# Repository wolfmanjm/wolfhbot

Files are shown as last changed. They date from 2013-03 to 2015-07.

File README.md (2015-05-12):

Wolf CoreXY
============

_NOTE_ This is still a work in progess, it is currently printing quite well.
_UPDATE_ Changed the Y rails to Makerslide and Makeslide carriages and VWheels.

A large build volume 3d printer based on the CoreXY concept.

It uses 2020 Misumi extrusions for most of the frame.

* The X carriage runs on 2020 and openrail from openbuilds.com
* The Y carraiges run on Makerslide from Inventables.com
* The drive can use either 65lb Spectra fishing line and machined spools, or GT2 pulleys and belts
* the Belts have no corss over, they are stacked on top of eachother instead
* build volume is around 12 inches cubed (300x300x300 mm)
* The Z platform has one Z actuator made of 2040 vslot
  and a printed carriage. It runs on an ACME 1/2" leadscrew with 10TPI and a printed PLA Nut
  and uses a moving knot to keep the cantilever level
* The X carriage is printable but is best milled from MDF

Pictures and Videos
-------------------

* [first movements](http://youtu.be/cA50g_V9wbQ)
* [second movement](http://youtu.be/p5AFRTE33c4)
* [Drawing big circle](http://youtu.be/9L7iuisqjXY)
* [Insane speed circle](http://youtu.be/wYBltiACMb0)
* [New Z actuator](http://flic.kr/p/gcBkjw)
* [New Z actuator](http://flic.kr/p/gcBGvX)
* [Printing vase](http://youtu.be/nGm1CWDJkY0)
* [Corexy Belt no cross over](http://flic.kr/p/iT5DkX)
* [Corexy Belt no cross over](http://flic.kr/p/iT7Lpm)
* [Corexy Belt no cross over](http://flic.kr/p/iT73UX)

For historical purposes...

* [animation of the scissor lift concept](http://blog.wolfman.com/files/scissor-lift.gif)
* [Scissor Lift prototype in action](http://youtu.be/5y0PBw3Y6yg)

Recently re wired to be Corexy rather than HBot. This seems to reduce
racking of the X Gantry. [See](http://joshuavasquez.com/docs/jVasquez/Projects/coreXY.html)

I see no difference between using Spectra line drive and GT2 belts, in
fact if anything it was slightly smoother using the line drive.

Spectra Drive
--------------
For Spectra drive the four idlers on the XGantry are grooved 5mm bearings that bolt
directly to the extrusion slots. One of the X carriage bearings is
raised 10mm to keep the lines parallel.

The four end idlers are grooved 5mm bearings that are screwed directly
into the tapped center of the vertical extrusion. This provides very
solid idlers than can take the tension of the spectra when it is
tight.  The grooves are necessary otherwise the spectra just runs off
the top or bottom of the bearing.
These bearings are stacked on top of each other with a
washer in between, this allows the cables to run on top of each other
and no cross over is needed.

GT2 Belt Drive
--------------
The two end idlers are 2x flanged bearings back to back, and another pair separated with a washer above it,
Then two of the idlers on the X Gantry are raised to keep the belt riding level.
I avoid the cross over of the belts by running the two belts one above the other in parallel.

Z Bed
-----

The scissor lift idea was nice but the prototype showed that a Nema17
did not have enough torque to lift the bed.  I think the bottom of the
scissor lift needs to lift 4 times the weight so any pressure on the
top caused the motor to skip.

The new Z actuator is a length of 500mm of 2040 VSlot, with a printed
carriage and v wheels. Driven by a McMaster ACME 1/2" leadscrew with
10TPI, Bearing blocks using 608 at top and bottom and a Nema17 with
5mm/0.25" flexible coupling. The bottom bearing block isolates the
flexible coupling from taking any weight and compressing. As the 1/2"
leadscrew is pretty big it has no wobble as far as I can tell and
having bearings top and bottom seems to be very stable. I also used a
printed Leadscrew nut printed in PLA and it seems pretty snug and
smooth. I also used a half height leadscrew nut and spring to implement
antibacklash which appears to be necessary.

There is a length of 2040 that spans from the Z actuator to the other
side of the frame where another 500mm length of 2040 VSlot has a vslot
mini carriage which is bolted to the end of the 2040 beam. Halfway
along this beam is a short piece of 2020 perpendicular to it, this
provides the third attachment point for the bed.

The most important part of this design is the
[moving knot](http://cockrum.net/cnc_mechanical.html), which is attached to
the top and bottom and runs over 4 v groove bearings on the cross
beam, This keeps the beam level while allowing a single actuator on one
end to move it up and down. This is the [far end](http://flic.kr/p/i67Sim),
and here is a view of the [whole assembly](http://flic.kr/p/i67Es7).

The bed is attached to the cross beam at three places to provide three
point bed levelling.  I use a scheme where a 4mm stud is screwed into
the tslots, and a 25mm length of aluminum rod, tapped to 4mm is
screwed onto that, this can be turned to move up and down the stud. At
the top of the aluminum is a cut out that the glass bed fits. Next to
this, and also bolted into the tslot, is an M4 bolt with a conical
spring bolted to the top, this pushes the glass at the three
attachment points up into the slots on the aluminum rounds. This keeps
the glass flat without deforming it, and allows it to be leveled at
three points by turning the aluminum rounds. Some jam nuts are used
to screw up to the aluminum rounds to stop them unscrewing once
levelled.

So this adds several printed parts... The Carriage, a bracket to hold
the leadscrew nut, and bearing blocks. Also some lathe work to cut a
thread into the center of some 1/2" aluminum round, and lathe a groove
at the top that the glass can slot into. (If the bed is not heated
this could be a printed part).

BOM
---
Aluminum parts are from Misumi with Misumi part numbers

* 10x 500mm HFS2020 20mm extrusions - frame
* 16x HBLFSN5 corner brackets - frame
* 2x  550mm HFS2020 - X Gantry sides
* 2x  85mm HFS2020 - X Gantry sides (Note it's cheaper to buy 2x 1000mm of 2020 and cut these yourself)
* 2x  540mm Makerslide - Y Rails
* 4x  HBLFSNF5 brackets - X Gantry
* 1x  500mm HFS2040 - Z Bed
* 1x  250mm HFS2020 - Z Bed
* 2x  Shapeoko motor mounts https://www.inventables.com/technologies/upgraded-shapeoko-motor-mount - Y carriages
* 12x VWheels https://www.inventables.com/technologies/dual-bearing-v-wheel-kit or http://openbuildspartstore.com/delrin-v-wheel-kit/
* lots of M5 nuts and bolts
* lots of M3 nuts and bolts
* 2x Nema 17 Stepper motors (preferably Kysan or equivalent)

Spectra drive
-------------
* 2x  Delrin Spools for [Spectra](http://3d.grabercars.com/?product=filament-drive-reel-grooved-delrin-18mm-o-d-for-kossel) or any of the spools he sells at http://3d.grabercars.com/?post_type=product
* 8x  625VV grooved bearings - for idlers from [ebay](http://www.ebay.com/itm/10-5-16-5mm-625VV-5mm-V-Groove-Guide-Pulley-Sealed-Rail-Ball-Bearing-5-16-5-/170998886188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)
* several yards of 65lb Spectra fishing line (Powerpro)
* 2x ball swivels from a fishing store

OR

Belt Drive
----------
* 10 meters GT2 belt
* 2 x GT2 pulleys 20 tooth
* 12 x 5mm flanged bearings for the idlers 

Printed Parts
-------------
* 1x motor-bracket-l.stl
* 1x motor-bracket-r.stl
* 1x x-carriage.stl

Z bed
-----
* 1x Nema 17
* 1x lead screw (McMaster 1/2" 10TPI ACME)
* Two printed Leadscrew nuts and a collar for the anti backlash
* 5/8" diameter spring for the anti backlash
* 2x 500mm 2040 VSlot
* 4x solid V Wheels http://openbuildspartstore.com/solid-v-wheel-kit/
* 1x printed Z carriage, plus leadnut holder
* 1x mini vslot carriage and mini wheels http://openbuildspartstore.com/mini-v-wheel-plate/
* 4x v groove bearings, 2x turnbuckles, two lengths of Spectra fishing line for the moving knot

Construction
------------

Getting the top of the frame square is essential, measure each end of the Y
rails to make sure they are parallel. Next the belts need to have exactly the
same tension to keep the X gantry straight, this was introducing non-square
prints for me. Loosen the X gantry on both Y carriages so it sits loosely on
the Y carriages, then measure the distance of each end of the X Gantry to the
front corner of the frame. Now tighten one or other belt until the X Gantry is
square to the Y rails, then tighten it down to the Y carriages.

If you find cylinders print out oblong or squares are not square this is
probably the problem.

License
-------

CC BY SA

<br /><span xmlns:dct="http://purl.org/dc/terms/" property="dct:title">WolfHBot</span> by <a xmlns:cc="http://creativecommons.org/ns#" href="http://wolfmanjm.github.com/wolfhbot" property="cc:attributionName" rel="cc:attributionURL">Jim Morris</a> is licensed under a <a rel="license" href="http://creativecommons.org/licenses/by-sa/3.0/deed.en_US">Creative Commons Attribution-ShareAlike 3.0 Unported License</a>.<br />Based on a work at <a xmlns:dct="http://purl.org/dc/terms/" href="https://github.com/wolfmanjm/wolfhbot" rel="dct:source">https://github.com/wolfmanjm/wolfhbot</a>.

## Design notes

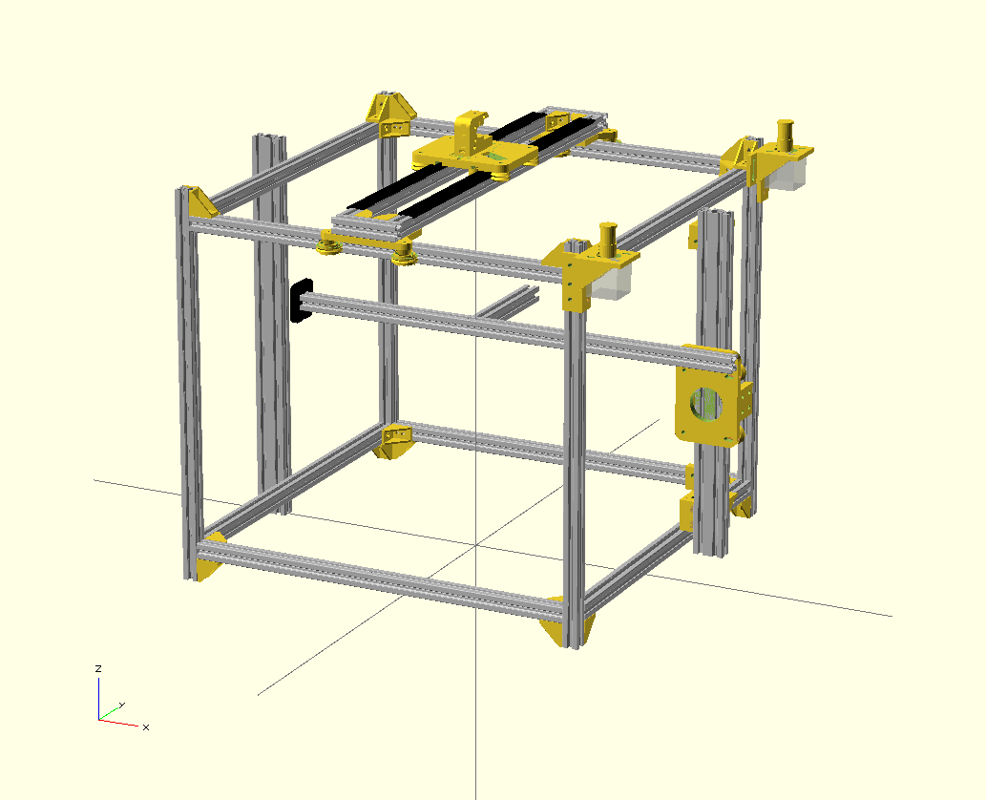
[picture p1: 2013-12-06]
pics/corexy-frame.png

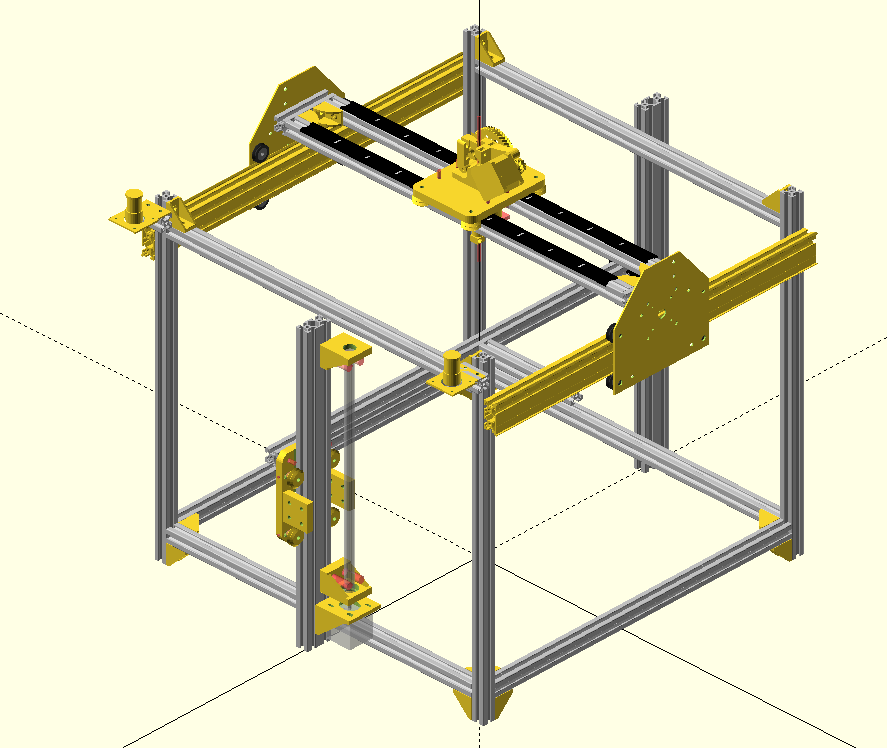
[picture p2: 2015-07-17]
pics/new-gantry.png

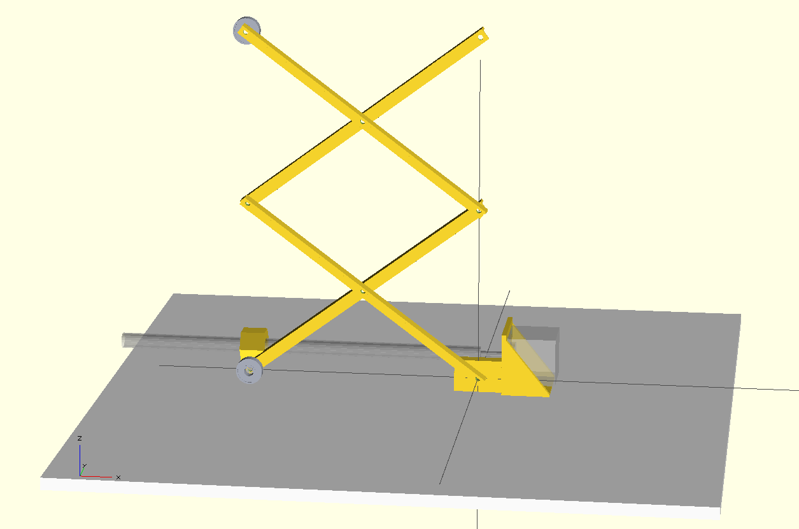
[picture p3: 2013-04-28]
pics/scissor-lift.png

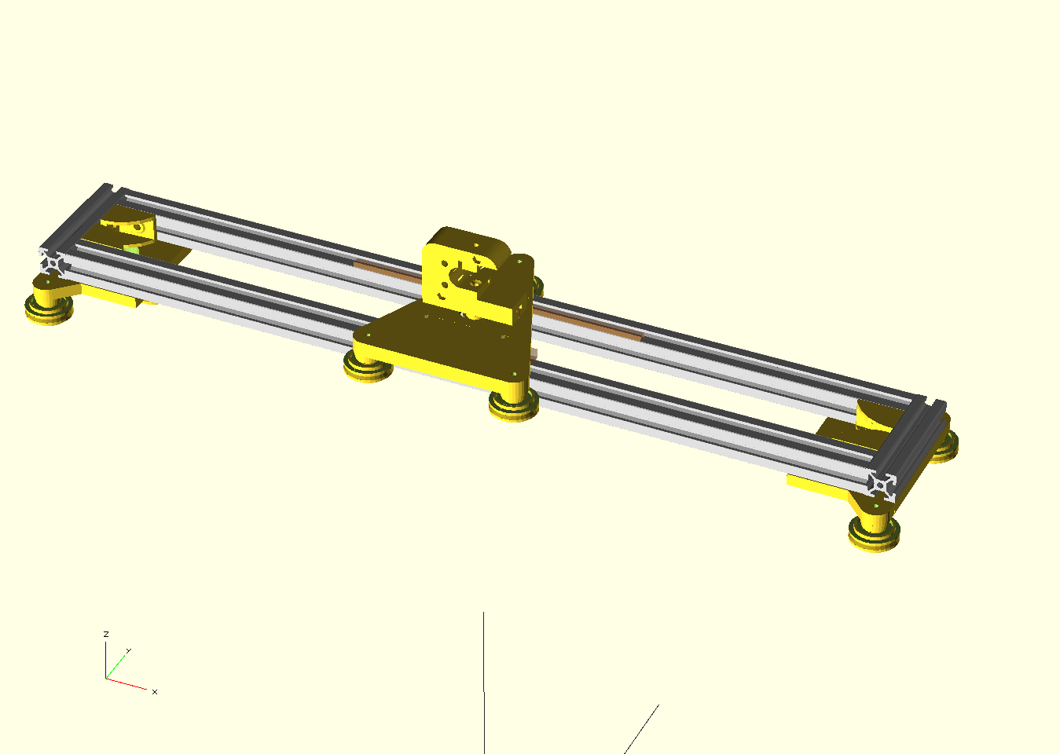
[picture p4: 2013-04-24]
pics/XYGantry.png

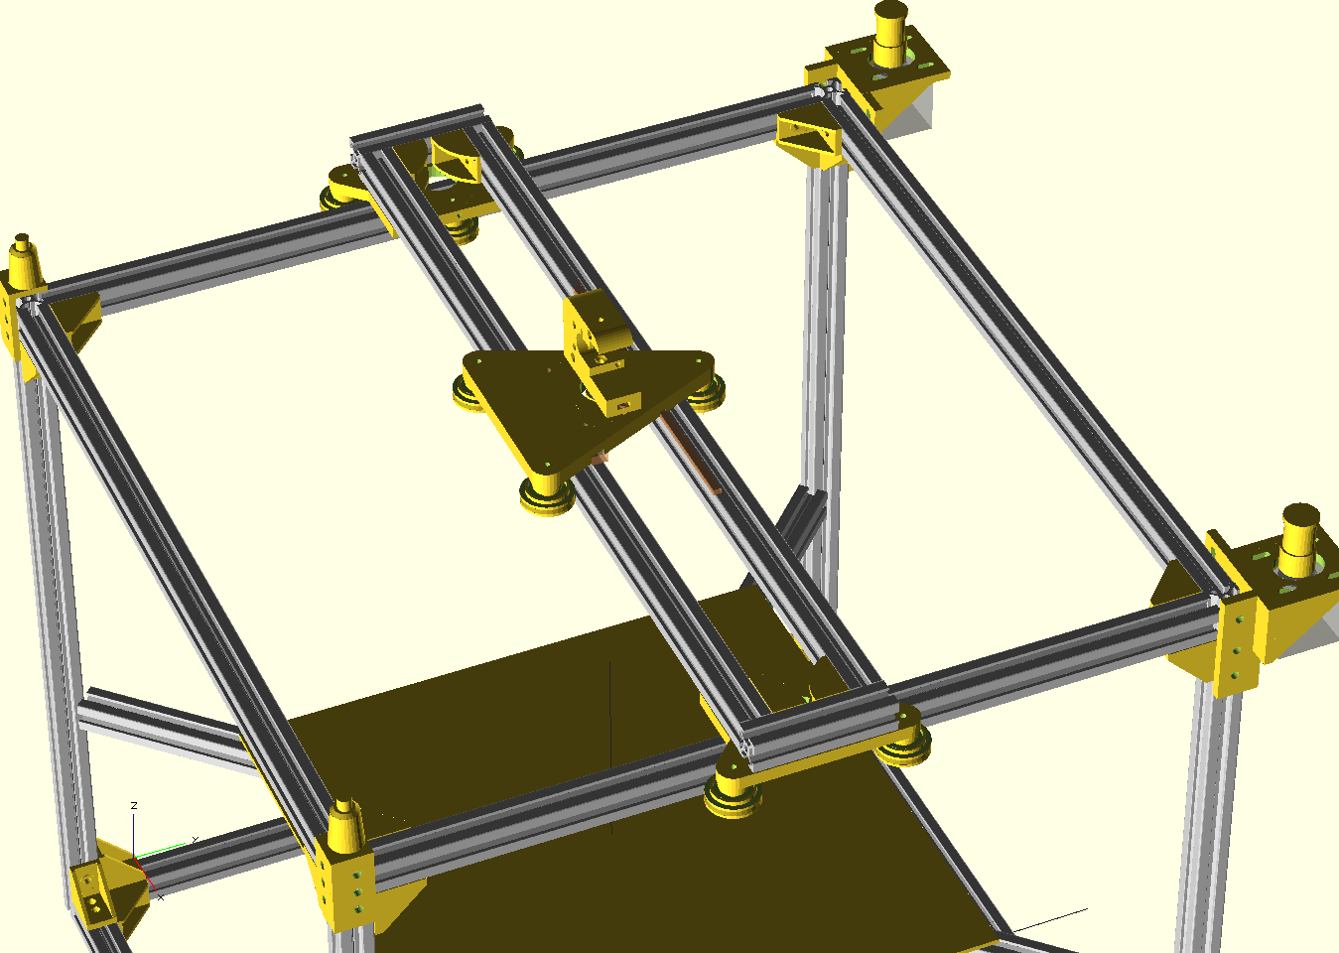
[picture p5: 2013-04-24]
pics/topview.png

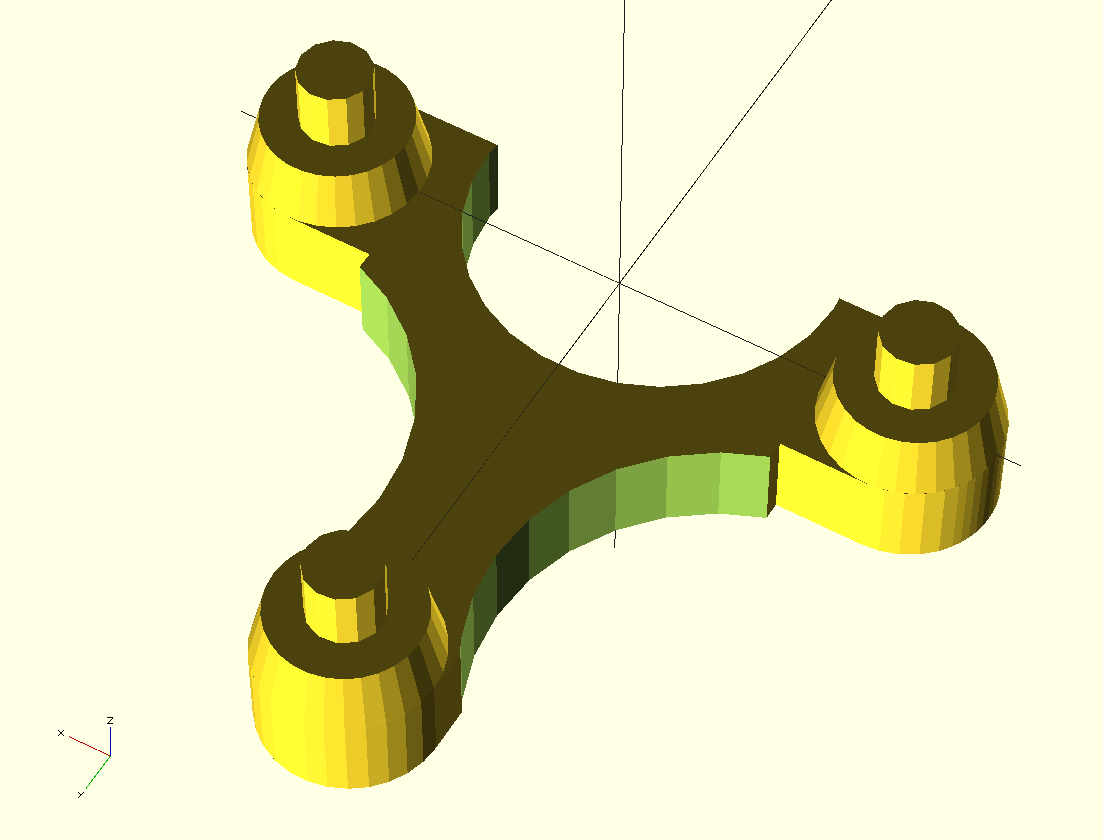
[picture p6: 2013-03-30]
steves-parametric-carriage.png

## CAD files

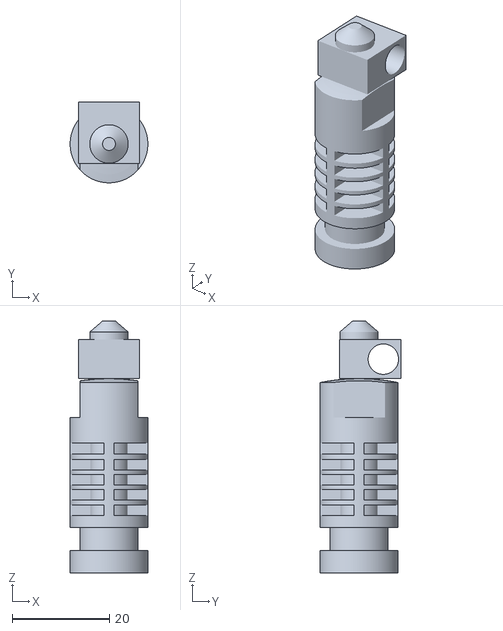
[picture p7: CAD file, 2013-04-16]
JHead_hotend_blank/jhead.stl
16.0 x 16.6 x 51.9

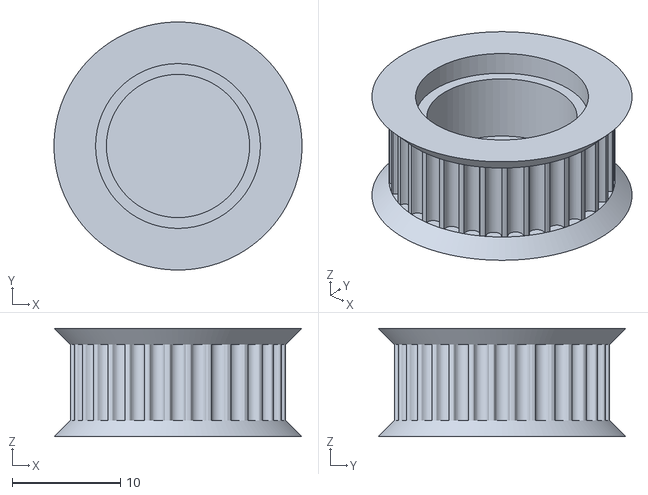
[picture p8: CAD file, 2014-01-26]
stl/GT2-pulley.stl
22.9 x 22.9 x 10.0

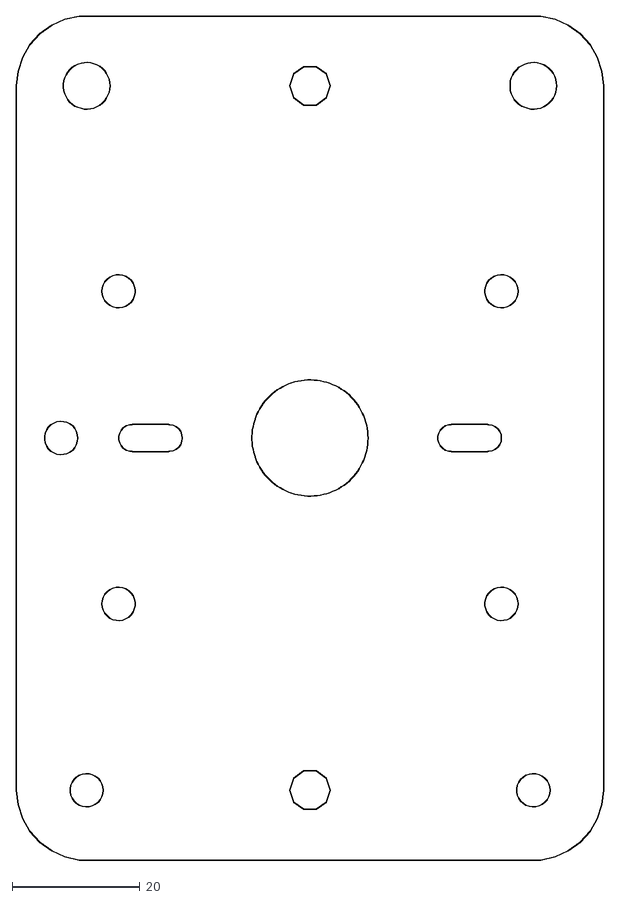
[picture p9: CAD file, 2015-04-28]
x-carriage-wide-alu.dxf
92.0 x 132.3

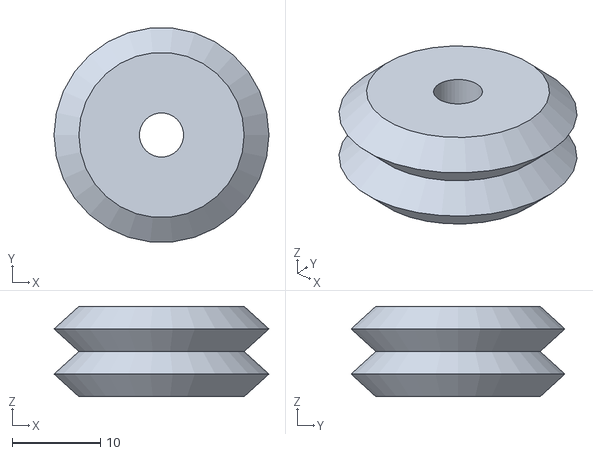
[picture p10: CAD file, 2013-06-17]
dual-v-wheel.stl
24.4 x 24.3 x 10.2

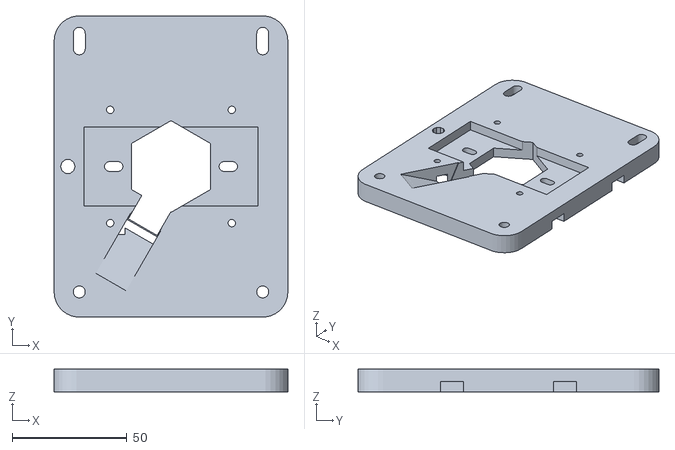
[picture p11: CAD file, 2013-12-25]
stl/x-carriage.stl
102.0 x 131.3 x 10.0

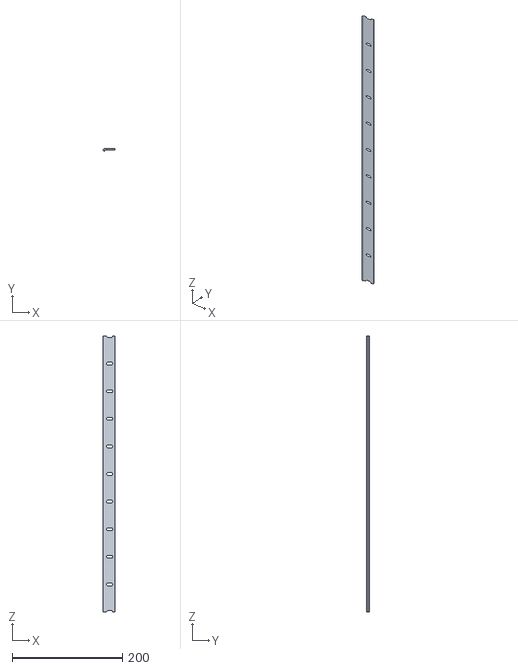
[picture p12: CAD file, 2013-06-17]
openrail500.stl
22.4 x 4.84 x 500.0

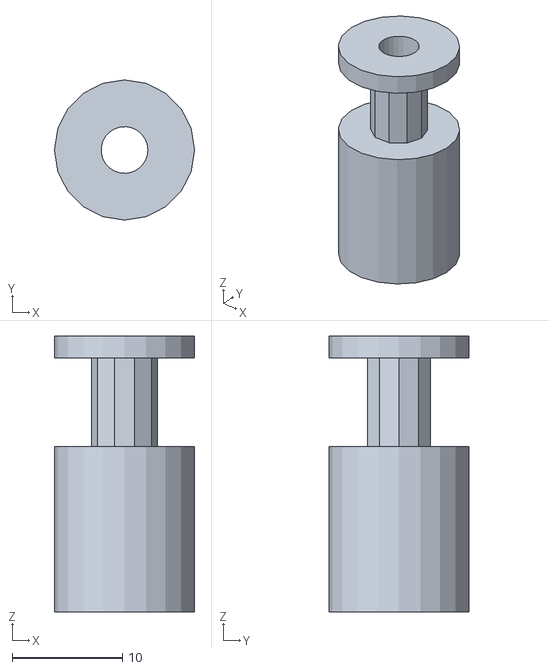
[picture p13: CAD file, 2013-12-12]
stl/bed-adjuster.stl
12.7 x 12.7 x 25.0

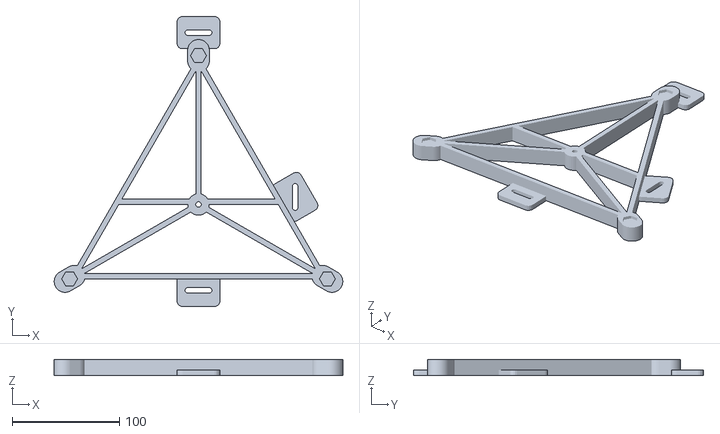
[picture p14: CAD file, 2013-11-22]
stl/bedleveller.stl
268.7 x 270.0 x 15.0

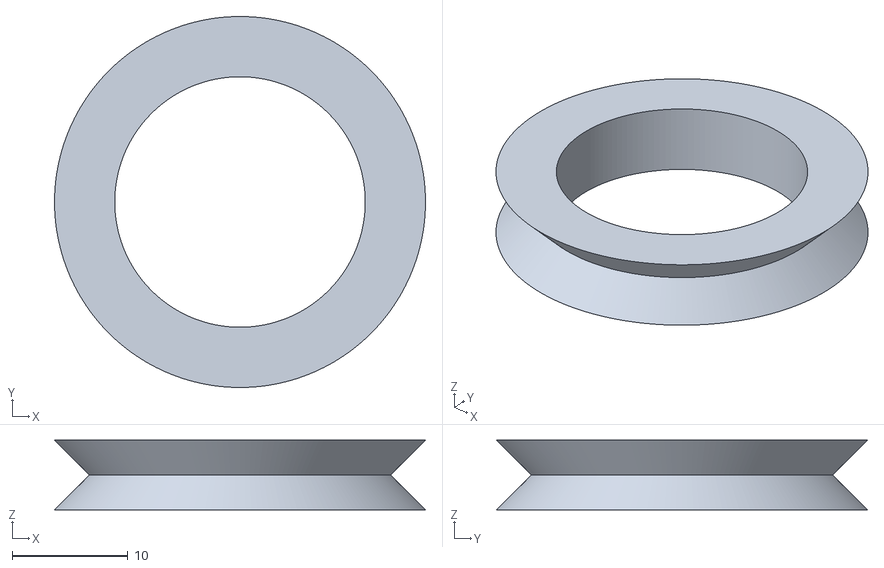
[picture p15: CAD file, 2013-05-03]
v-wheel.stl
32.0 x 32.0 x 6.00

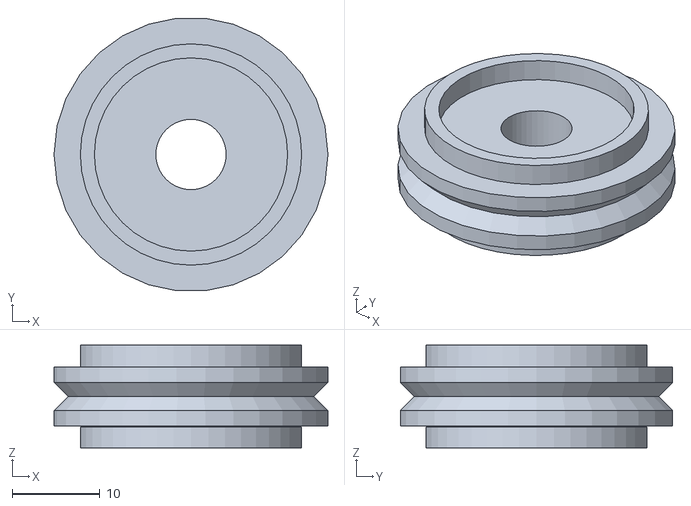
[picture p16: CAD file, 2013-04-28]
w-wheel.stl
31.2 x 31.0 x 11.7

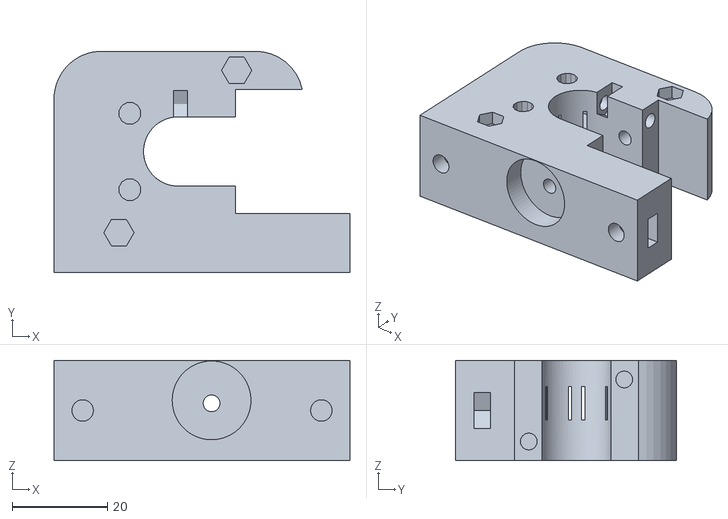
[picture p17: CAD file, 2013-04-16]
me_body_v5.2_3mm.stl
62.0 x 46.4 x 21.0

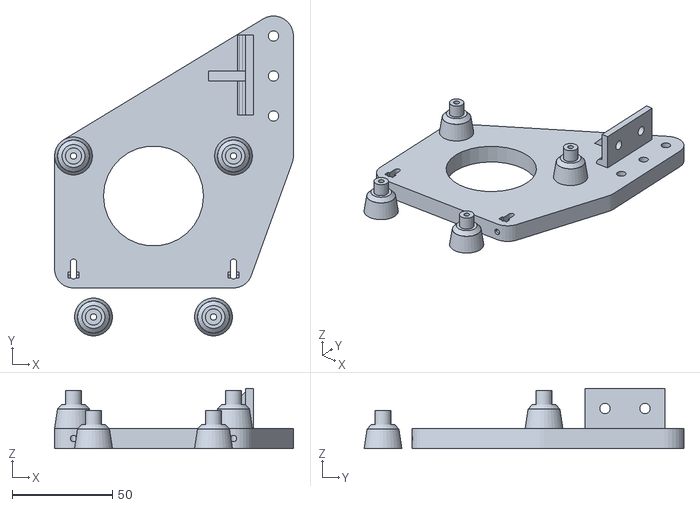
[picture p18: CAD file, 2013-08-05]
stl/z-carriage-4wheel.stl
119.5 x 159.9 x 30.0

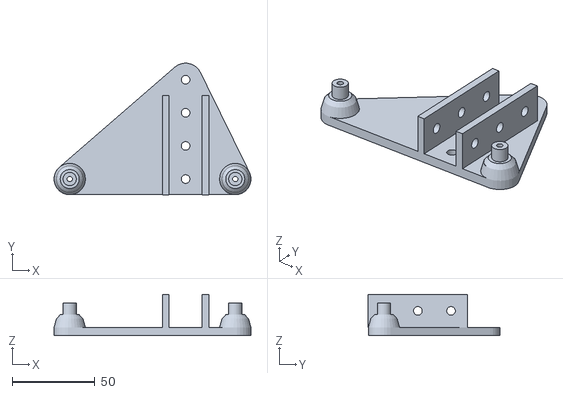
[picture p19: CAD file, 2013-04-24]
stl/z-carriage.stl
119.0 x 79.4 x 24.9

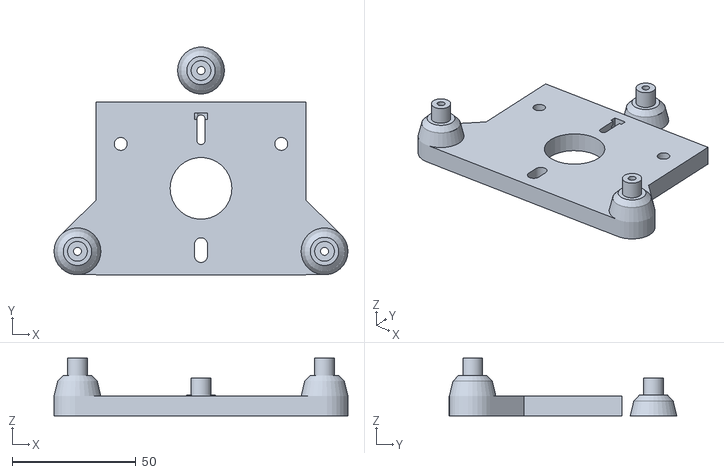
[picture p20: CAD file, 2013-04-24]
stl/y-carriage.stl
119.0 x 92.1 x 23.5

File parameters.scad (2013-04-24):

use <w-wheel.scad>

// the dimensions of the extrusion to run on
extrusion_width= 20; // the side that the wheels run on
extrusion_height= 20;
extrusion= 20; // the smaller of the two dimensions

wheel_diameter = w_wheel_dia();
wheel_width= w_wheel_width();
wheel_id= w_wheel_id();
wheel_indent= w_wheel_indent();

pillardia= 19;

bearingThickness= 7;
bearingOD= 22;
bearingID= 8;
bearingShaftCollar= 11.5;

sides= 500; // side length of frame in mm
height= sides-extrusion/2; // height of frame

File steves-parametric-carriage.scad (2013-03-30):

use <misumi-parts-library.scad>
use <w-wheel.scad>

// the dimensions of the extrusion to run on
extrusion_width= 20; // the side that the wheels run on
extrusion_height= 20;

// the thickness of the base
thickness = 10;

wheel_distance= 66; // distance from wheel center to center of top two wheels

wheel_diameter = w_wheel_dia();
wheel_width= w_wheel_width();
wheel_id= w_wheel_id();

bearingThickness= 7;
bearingOD= 22;
bearingID= 8;

wheel_clearance= 2; // clearance between the side of the extrusion and the carriage
pillarht= extrusion_height/2-wheel_width/2+wheel_clearance;
pillardia= 19;
clearance= 0; // increase for more clearance, decrease for tighter fit
wheel_separation= extrusion_width+wheel_diameter+clearance; // separation of two wheels and bottom wheel for given extrusion

Ycarriage();

wheel_z= pillarht+wheel_width/2;
%translate([-wheel_distance/2, 0, wheel_z]) w_wheel();
%translate([wheel_distance/2, 0, wheel_z]) w_wheel();
%translate([0, wheel_separation, wheel_z]) w_wheel();


%translate([200/2, wheel_separation/2, wheel_z]) rotate([0, 0, 90]) hfs2020(200);

function get_wheel_z()= wheel_z;

// used to clean the base around the pillar using an intersection
module wheel_pillar_cutout(h=thickness) {
	translate([0,0,-thickness/2]) union() {
		cylinder(r=pillardia/2, h=h, center=true);
		translate([0, -100/2, 0]) cube([pillardia,100,h], center=true);
		translate([0, -200/2-pillardia/2, 0]) cube([200,200,h], center=true);
	}
}

module wheel_pillar(){
	ht= pillarht;
	translate([0,0,ht/2]) union() {
		cylinder(r1=pillardia/2, r2=16/2, h=ht, center=true);
		translate([0,0,ht/2]) cylinder(r=bearingID/2, h=bearingThickness);
	}
}

module base() {
	r= pillardia/2;
	difference() {
		translate([0,0,-thickness]) linear_extrude(height= thickness) hull() {
			translate([-wheel_distance/2,0,0]) circle(r= r);
			translate([wheel_distance/2,0,0]) circle(r= r);
			translate([0,wheel_separation,0]) circle(r= r);
		}
		translate([wheel_separation/2+6,wheel_distance/2+2,-thickness-0.1]) cylinder(r=50/2, h= thickness+0.2);
		translate([-wheel_separation/2-6,wheel_distance/2+2,-thickness-0.1]) cylinder(r=50/2, h= thickness+0.2);
		translate([0,-8,-thickness-0.1]) cylinder(r=40/2, h= thickness+0.2);
	}
}

module Ycarriage() {
	union() {
		intersection() {
			base();
			translate([0,wheel_separation,0]) wheel_pillar_cutout();
			translate([-wheel_distance/2,0,0]) rotate([0,0,90]) wheel_pillar_cutout();
			translate([wheel_distance/2,0,0]) rotate([0,0,-90]) wheel_pillar_cutout();
		}
		translate([-wheel_distance/2,0,0]) wheel_pillar();
		translate([wheel_distance/2,0,0]) wheel_pillar();
		translate([0,wheel_separation,0]) wheel_pillar();
	}
}

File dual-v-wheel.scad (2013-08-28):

// openbuilds dual v wheel
od= 24.39;
id= 18.75;

t= 5.12; // thickness of one half
thick= 10.23;

wheel_id= id; // the diameter of the outside hole
wheel_d= 0; // the depth from the outside of the wheel to the bearing
wheel_groove_d= 0; // the depth of the groove on the outside of the wheel
wheel_groove_w= 0; // the width of the groove on the outside of the wheel

bearingThickness= 5;
bearingOD= 16;
bearingID= 5;
shim= 1;

function v_wheel_dia()= od;
//function v_wheel_width()= thick;
function v_wheel_width()= bearingThickness*2+shim; // includes bearing
function v_wheel_id()= wheel_id;
function v_wheel_indent()= wheel_d-0.1;

module V_wheel() {
	cylinder(r1=od/2,r2=id/2, h=t/2);
	translate([0,0,t/2]) cylinder(r2=od/2,r1=id/2, h=t/2);
	translate([0,0,t]) cylinder(r1=od/2, r2=id/2, h= t/2);
	translate([0,0,-t/2]) cylinder(r2=od/2, r1=id/2, h= t/2);
}

module groove() {
	// make a negative of the cutout so it can be differenced
	difference() {
		cylinder(r=od/2+0.1, h=wheel_groove_d+0.1, $fn=40);
		cylinder(r=od/2-wheel_groove_w, h=wheel_groove_d, $fn=40);
	}
}

module v_wheel() {
	difference() {
		translate([0,0,-t/2]) V_wheel();
		translate([0,0,-(thick+4)/2]) cylinder(r=bearingID/2, h=thick+4, $fn=40);
	}
}

module v_wheel_vertical() {
	rotate([0,90,0]) v_wheel();
}

v_wheel();
//w_wheel_vertical();
//V_wheel();

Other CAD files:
stl/idlercollar-605.stl
stl/idlercollar-608.stl
stl/motor-bracket-r.stl
stl/motor-bracket-l.stl
GT2-idler.scad
JHead_hotend_blank/jhead.scad
Thread_Library.scad
XGantry-40.scad
XGantry-60.scad
XGantry-wide.scad
bed-adjuster.scad
bed.scad
bedleveller.scad
bend.scad
eccentric-cam.scad
endstop-holder.scad
hbot-frame.scad
hotend-extender.scad
idler-corner.scad
idler-gantry.scad
idler.scad
lead-nut-connector.scad
leadscrew-bearing-block.scad
leadscrewnut_0.5in-10tpi.scad
leadscrewnut_0.5in.scad
misumi-parts-library.scad
misumi/hbl135td5.stl
misumi/hbl135ts5.stl
misumi/hbl45ts5.stl
motor-bracket.scad
motor-mount.scad
myLibs.scad
openrail.scad
openrailwheel.scad
rail-bracket.scad
scissor-lift.scad
sg-spool.scad
squirrel-fan.scad
src/XGantry.scad
src/bed.scad
src/corner-bracket.scad
src/eccentric-cam.scad
src/hbot-frame.scad
src/idler-corner.scad
src/idler-gantry.scad
src/idler.scad
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

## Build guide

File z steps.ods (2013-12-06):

mm/rotation | steps/rotation | microsteps | length | h | d | minh | maxd
2.54 | 3200 | 16 | 165 | 200 | 10 | 72.9451848993 | 148
layer ht | steps/mm | mm/step | tiers |  |  | min | max
0.3 | 1259.842519685 | 0.000793750 | 1 |  | max error between | 65 | 320 | mm | 216 | $H$216
 |  | 0.012700000 |  |  | 0.00444 |  |  |  | 1066 | $H$1066
 |  |  |  | max d | 299.48295 | travel |  |  |  |  |  | max error
 |  |  |  | min d | 0.00007 | 299.4828876009 |  |  |  |  |  | 0.00039375
 |  | 165
layer ht | h | d | Absolute steps | actual step | actual d | actual h | error in ht mm |  | steps | actual steps | actual move | error
0.3 | 0.15 | 164.9999318182 | 0.0858983714 | 0 | 165 | 0 | 0.15 |  | 377.9527559055 | 378 | 0.3000375 | 0.0000375
0.6 | 0.3 | 164.9997272725 | 0.3435936984 | 0 | 165 | 0 | 0.3 |  | 755.905511811 | 756 | 0.600075 | 0.000075 | 0.000075
0.9 | 0.45 | 164.9993863625 | 0.7730866201 | 1 | 164.99920625 | 0.5117976846 | 0.0617976846 |  | 1133.8582677165 | 1134 | 0.9001125 | 0.0001125 | 0.0001125
1.2 | 0.6 | 164.9989090873 | 1.3743782012 | 1 | 164.99920625 | 0.5117976846 | 0.0882023154 |  | 1511.8110236221 | 1512 | 1.20015 | 0.00015 | 0.00015
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

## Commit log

2013-03-29 added some new files
    [bed.scad, hblfsd5.stl, hblfsn5.stl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]
2013-03-29 add stl
2013-03-30 add carriage
    [w-wheel.scad, w-wheel.stl, y-carriage.scad]
2013-03-30 add steves parametric carriage
    [steves-parametric-carriage.scad, w-wheel.scad]
2013-03-30 add x gantry
    [XGantry.scad, w-wheel.scad, y-carriage.scad]
2013-03-30 add flanges to hold 2020 to y carriage
    [XGantry.scad, hbot-frame.scad, y-carriage.scad]
2013-03-30 add src
    [XGantry.scad, hbot-frame.scad, w-wheel.scad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]
2013-03-30 use local myLibs
    [y-carriage.scad]
2013-04-02 added stuff
    [corner-bracket.scad, hbot-frame.scad, motor-mount.scad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]
2013-04-06 added adjustabke y carriage
    [eccentric-cam.scad, my-wheel.scad, y-carriage.scad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]
2013-04-07 made gantry wider from two lengths of extrusion turned Y carriages on their side added tightening screw to third wheel on y carriage
    [XGantry.scad, hbot-frame.scad, y-carriage.scad]
2013-04-16 added x carriage updated gantry
    [XGantry.scad, hbot-frame.scad, jhead.scad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]
2013-04-16 added motor bracket
    [motor-bracket.scad]
2013-04-17 added new objects motor mount and sg-spool
    [XGantry.scad, bed.scad, hbot-frame.scad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]
2013-04-20 added idlers and stls
    [idler-605.stl, idler-corner.scad, idler-corner.stl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]
2013-04-21 updated x-carriage
    [x-carriage.scad, x-carriage.stl]
2013-04-22 new type of idler for spectra, just collars and spectra runs on bearing surface
    [idler-608.stl, idler.scad, idlercollar-605.stl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]
2013-04-22 remove v idlers they don't work too well with spectra
    [idler-605.stl, idler-608.stl]
2013-04-23 updated Y carriage to allow X gantry to boolt on top of it
    [y-carriage.scad]
2013-04-23 make ycarriage wheels further apart for stability
    [XGantry.scad, y-carriage.scad]
2013-04-24 added pics updated overall scad updated y-carriage
    [hbot-frame.scad, y-carriage.scad]
2013-04-24 updated stls
    [x-carriage.stl, y-carriage.stl]
2013-04-24 added z-carriage updated bed and frame
    [bed.scad, hbot-frame.scad, parameters.scad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]
2013-04-25 update with z platform runners
    [bed.scad, hbot-frame.scad]
2013-04-25 Add BoM to readme
2013-04-25 added printed parts to BoM
2013-04-28 added scissor lift
    [bed.scad, hbot-frame.scad, scissor-lift.scad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]
2013-04-28 added leadscrew nut and associated thread library added scissor lift pics
    [Thread_Library.scad, hbot-frame.scad, leadscrewnut_0.5in.scad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]
2013-05-01 added a three wheel z carriage with raised platform
    [bed.scad, hbot-frame.scad, scissor-lift.scad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]
2013-05-01 added cap plate to scissor lift
    [scissor-lift.scad]
2013-05-03 add v wheel
    [v-wheel.stl]
2013-06-13 move side rails down
    [hbot-frame.scad]
2013-06-16 change 45 degree distance for extrusion to measured distance add triangle to my libs
    [myLibs.scad, z-carriage-3wheel.scad]
2013-06-17 added new x carriage with 4 wheels for openrail made z carriage mirror and adjusted bed for mirrored version added openrail v wheel
    [bed.scad, dual-v-wheel.scad, dual-v-wheel.stl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]
2013-06-21 added squilrrel fan model
    [squirrel-fan.scad]
2013-06-21 update x carriage for open rail
    [x-carriage-new.scad]
2013-06-21 use bushings as standoffs for v wheels
    [x-carriage-new.scad]
2013-06-22 add openrail to x gantry invert xgantry
    [XGantry.scad, eccentric-cam.scad, hbot-frame.scad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]
2013-07-14 add z gantry concept
    [bed.scad, hbl135td5.stl, hbl135ts5.stl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]
2013-07-15 new z gantry
    [hbot-frame.scad, z-leadscrew-gantry.scad]
2013-07-15 Added a 4 wheel z carriage
    [z-carriage-4wheel.scad]
2013-07-19 added new x carriage
    [bed.scad, x-carriage-new.stl, z steps.ods]
2013-08-05 added z carriage for vslot stl
    [z-carriage-4wheel.stl]
2013-08-28 make vwheel actual width including bearings
    [dual-v-wheel.scad]
2013-09-01 add a gt2 z gantry modify the lead screw z gantry
    [z-gt2-gantry.scad]
2013-09-03 new version of gantry
    [z-leadscrew-gantry-v2.stl, z-leadscrew-gantry.scad]
2013-09-12 adde bearing block for lead screw
    [leadscrew-bearing-block.scad, motor-mount.scad, z-leadscrew-gantry.scad]
2013-09-28 added 10tpi leadscrew Added bearing block for z actuator
    [lead-nut-connector.scad, lead-nut-connector.stl, leadscrew-bearing-block.scad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]
2013-11-22 update with new pic
    [bed.scad, hbot-frame.scad, z steps.ods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]
2013-11-22 added the bed leveller
    [bedleveller.scad]
2013-11-22 beefed up bedleveller
    [bed.scad, bedleveller.scad, bedleveller.stl]
2013-12-12 added the bed leveller spacer added anti backlash to lead-nut-connecoter
    [bed-adjuster.scad, bed-adjuster.stl, lead-nut-connector.scad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]
2013-12-14 added holders for endstops and magnets
    [bend.scad, endstop-holder.scad]
2013-12-25 ne x carriage
    [x-carriage-new.stl, x-carriage.stl]
2014-01-03 updated readme new XGantry WIP
    [XGantry.scad, x-carriage.scad, y-carriage.scad]
2014-01-08 added various types of x carriage and new X gantry
    [XGantry-40.scad, XGantry-60.scad, XGantry-wide.scad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]
2014-01-21 new style with hotend extender
    [XGantry-wide.scad, x-carriage-wide.scad]
2014-01-26 added the gt2 idlers added the hotend extender
    [GT2-pulley.stl, Pulley_T-MXL-XL-HTD-GT2_N-tooth.scad, hotend-extender.scad]
2014-02-04 added idler
    [GT2-idler.scad]
2014-03-26 add millable carriage
    [endstop-holder.scad, x-carriage-wide-alu.dxf]
